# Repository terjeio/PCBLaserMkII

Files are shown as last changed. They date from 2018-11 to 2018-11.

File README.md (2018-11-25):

## BluRay Laser PCB exposer

---

### Design criteria:

160 x 100mm exposure area \(Eurocard\).
Able to render at least down to 0.25mm \(10 mil, 250um\) track/track separation.
Easy workflow.

### Vector vs. raster plotting:

Vector plotting requires parsing of a vector format to control the drive mechanism,
most PCB-design packages are able to output the design in Gerber and/or HPGL-formats.

Raster plotting is similar to inkjet printing, the laser is fired for the individual pixels.

I decided to use raster plotting since this is relatively simple to implement.

By using the belt calculator available at [buildlog.net](http://buildlog.net/cnc_laser/belt_calcs.htm) I found that
17 teeth pulleys and 8 microsteps would result in a resolution of 1195.297 steps per inch, which is pretty close to 1200 dpi \(21.250 um/step\). Near enough for hobby use, resolution may be adjusted when generating the bitmap file to match the actual resolution if a perfect match is required.

### Photosentive PCBs:

I had some blank PCBs lying around so I wanted to try Dupont Riston dry-film photoresist.
This has optimal sensitivity in the 350-380nm range, and may be exposed by 405nm as there is some sensitivity up to 450nm.
Lines and spaces achievable:
In optimized production environment: 75um/3mil
In lab environment: 50um/2mil

The (teoretical) resolution of the design is thus somewhat better than the resolution of the film.

### Workflow for KiCad EDA:

Plot the design to PDF in 1:1 format. Print resulting files via PDFCreator to PNG-format files, I use 4bpp in order to avoid artefacts in the bitmap.

### Firmware:

[Firmware](https://github.com/terjeio/PCBLaserFirmvare/) is provided for [MSP430G2553 LaunchPad](http://www.ti.com/tool/MSP-EXP430G2) or MSP430F5310 on a [custom PCB](Electrical/Controller). The MSP430F5310 is slightly faster and has more RAM, useful for buffering. It also supports adjusting the laser power via the [desktop application](https://github.com/terjeio/PCBLaserDesktopApp).

Firmware may be compiled in the [cloud](https://dev.ti.com), there is no need to install a local IDE.

### Hackaday project:

[PCB Exposer](https://hackaday.io/project/26216-pcb-exposer)

### Improvements:

A closed design with an interlocked door to block reflections from the laser. The published version is an open design, **ALWAYS** use protective eyewear when operating the exposer!

Laser cut acrylic bed? My prototype has an aluminium bed that requires access to a mill to fabricate. 

---

BOM:
<pre>
3 SC6UU 25x30x18 polymer bearing in aluminium housing
2 LM6UU 5x10x14 polymer bearing (or Oilite sintered bronze bearings)
4 6mm ground shafts, 300mm
2 3mm ground shafts or similar, 25mm for the belt idlers
1 3D printed laser carrier, FreeCAD design provided
1 diode housing 13x16x15,5
1 lens 405nm 8mm focal length?
1 405nm laser diode, 100mW
2 Nema 17 stepper motors, max 34mm long
2 17T pulleys
2 idlers to match the pulleys
  GT2 6mm belt, approx. 1m
  6mm acrylic for laser cut case, dxf-files provided
  4mm acrylic for laser cut case, dxf-files provided
1 MSP430G2553 LaunchPad or custom controller PCB (design included). Please refer to schematics for BOM for the latter.
1 laser driver PCB (design included). Please refer to schematics for BOM.
</pre>

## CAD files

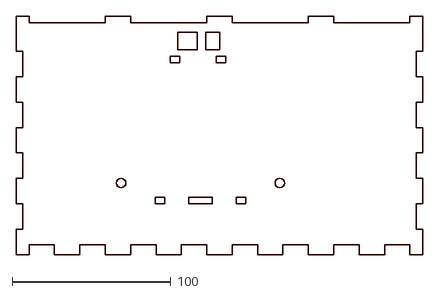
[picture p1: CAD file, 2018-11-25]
Mechanical/Back 4mm.dxf
256.0 x 150.0

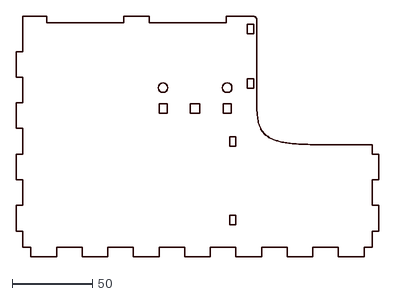
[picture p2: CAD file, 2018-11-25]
Mechanical/Left side 4mm.dxf
226.0 x 150.0

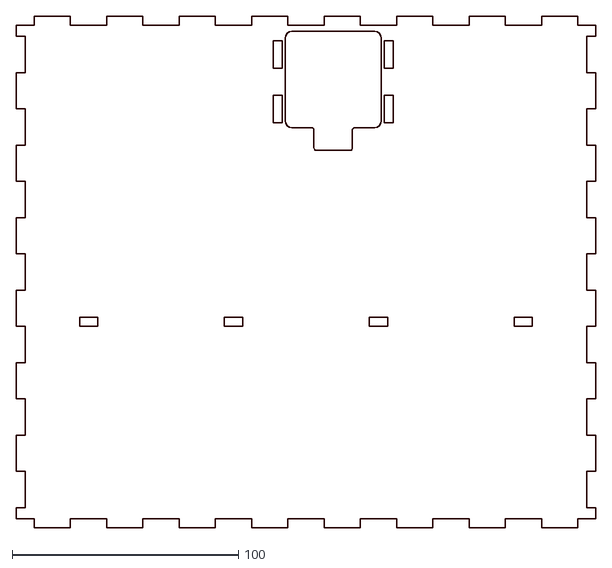
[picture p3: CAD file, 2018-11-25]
Mechanical/Base 6mm.dxf
256.0 x 226.0

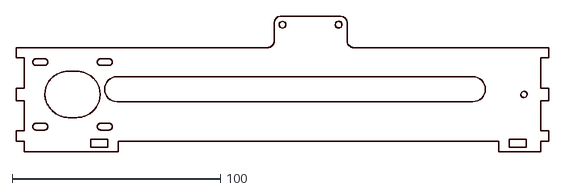
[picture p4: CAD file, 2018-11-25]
Mechanical/X-motor bracket 6mm.dxf
256.0 x 65.0

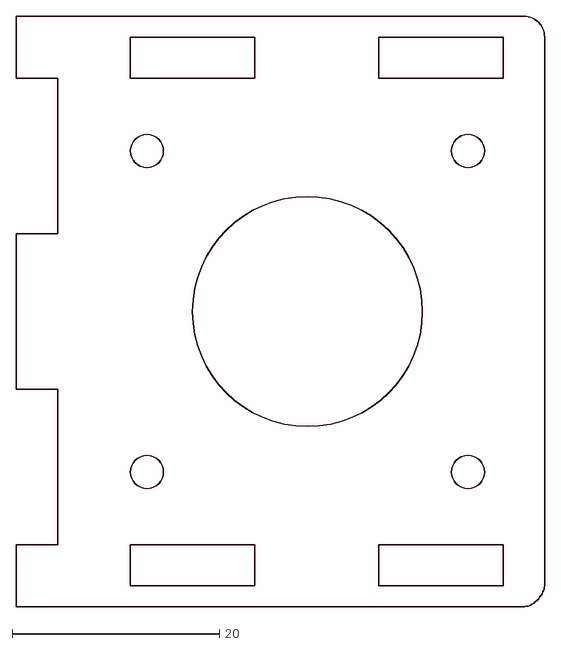
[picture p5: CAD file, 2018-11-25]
Mechanical/Y-motor bracket top 4mm.dxf
51.0 x 57.0

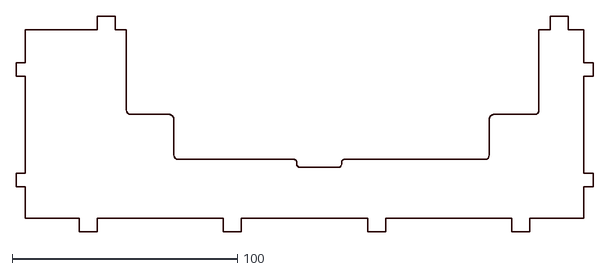
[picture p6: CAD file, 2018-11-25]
Mechanical/Wall stiffener 4mm.dxf
256.0 x 95.5

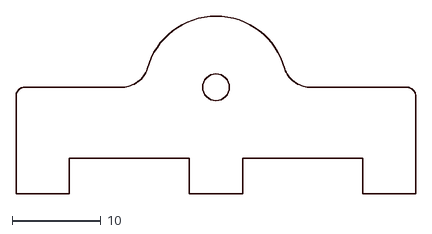
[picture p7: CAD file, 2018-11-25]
Mechanical/X-idler holder 4mm.dxf
45.0 x 20.0

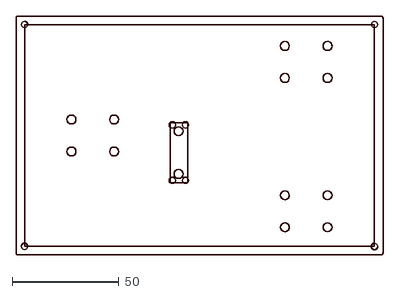
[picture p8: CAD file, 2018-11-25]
Mechanical/Alu bed.dxf
172.0 x 112.0

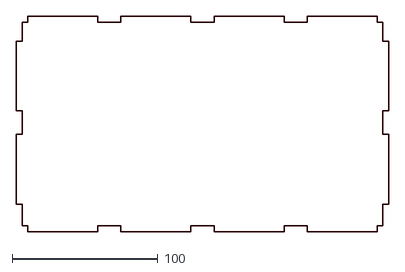
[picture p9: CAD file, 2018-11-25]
Mechanical/Top 4mm.dxf
256.0 x 148.0

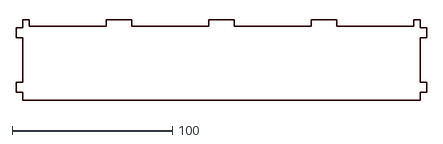
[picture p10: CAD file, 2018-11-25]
Mechanical/Front recessed 4mm.dxf
256.0 x 50.0

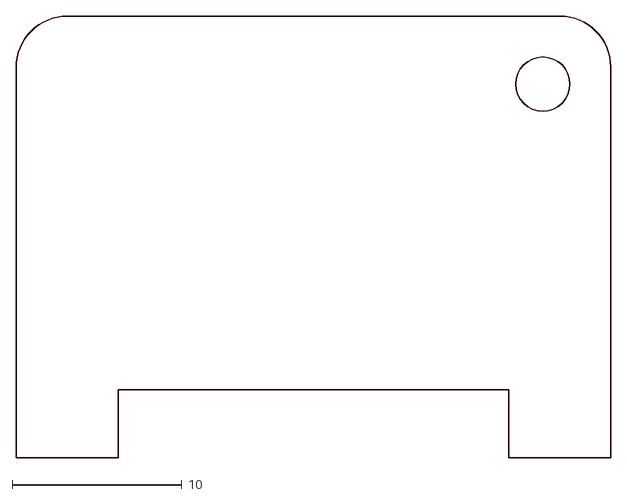
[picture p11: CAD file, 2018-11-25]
Mechanical/PCB bracket 4mm.dxf
35.0 x 26.0

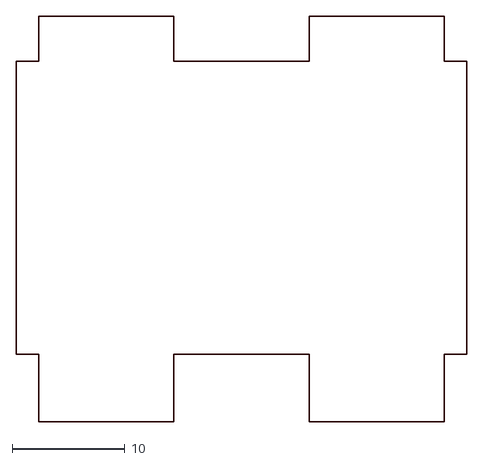
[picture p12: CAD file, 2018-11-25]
Mechanical/Y-motor bracket side 4mm (x2).dxf
40.0 x 36.0

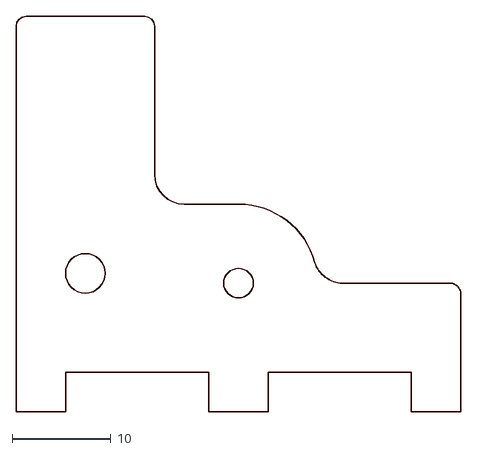
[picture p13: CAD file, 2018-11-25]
Mechanical/Y-idler holder #1 4mm.dxf
45.0 x 40.0

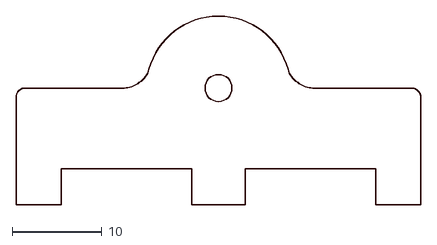
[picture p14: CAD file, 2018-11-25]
Mechanical/Y-idler holder #2 4mm.dxf
45.0 x 21.0

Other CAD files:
Mechanical/Right side 4mm.dxf
Mechanical/laser head.FCStd
Mechanical/Front 4mm.dxf

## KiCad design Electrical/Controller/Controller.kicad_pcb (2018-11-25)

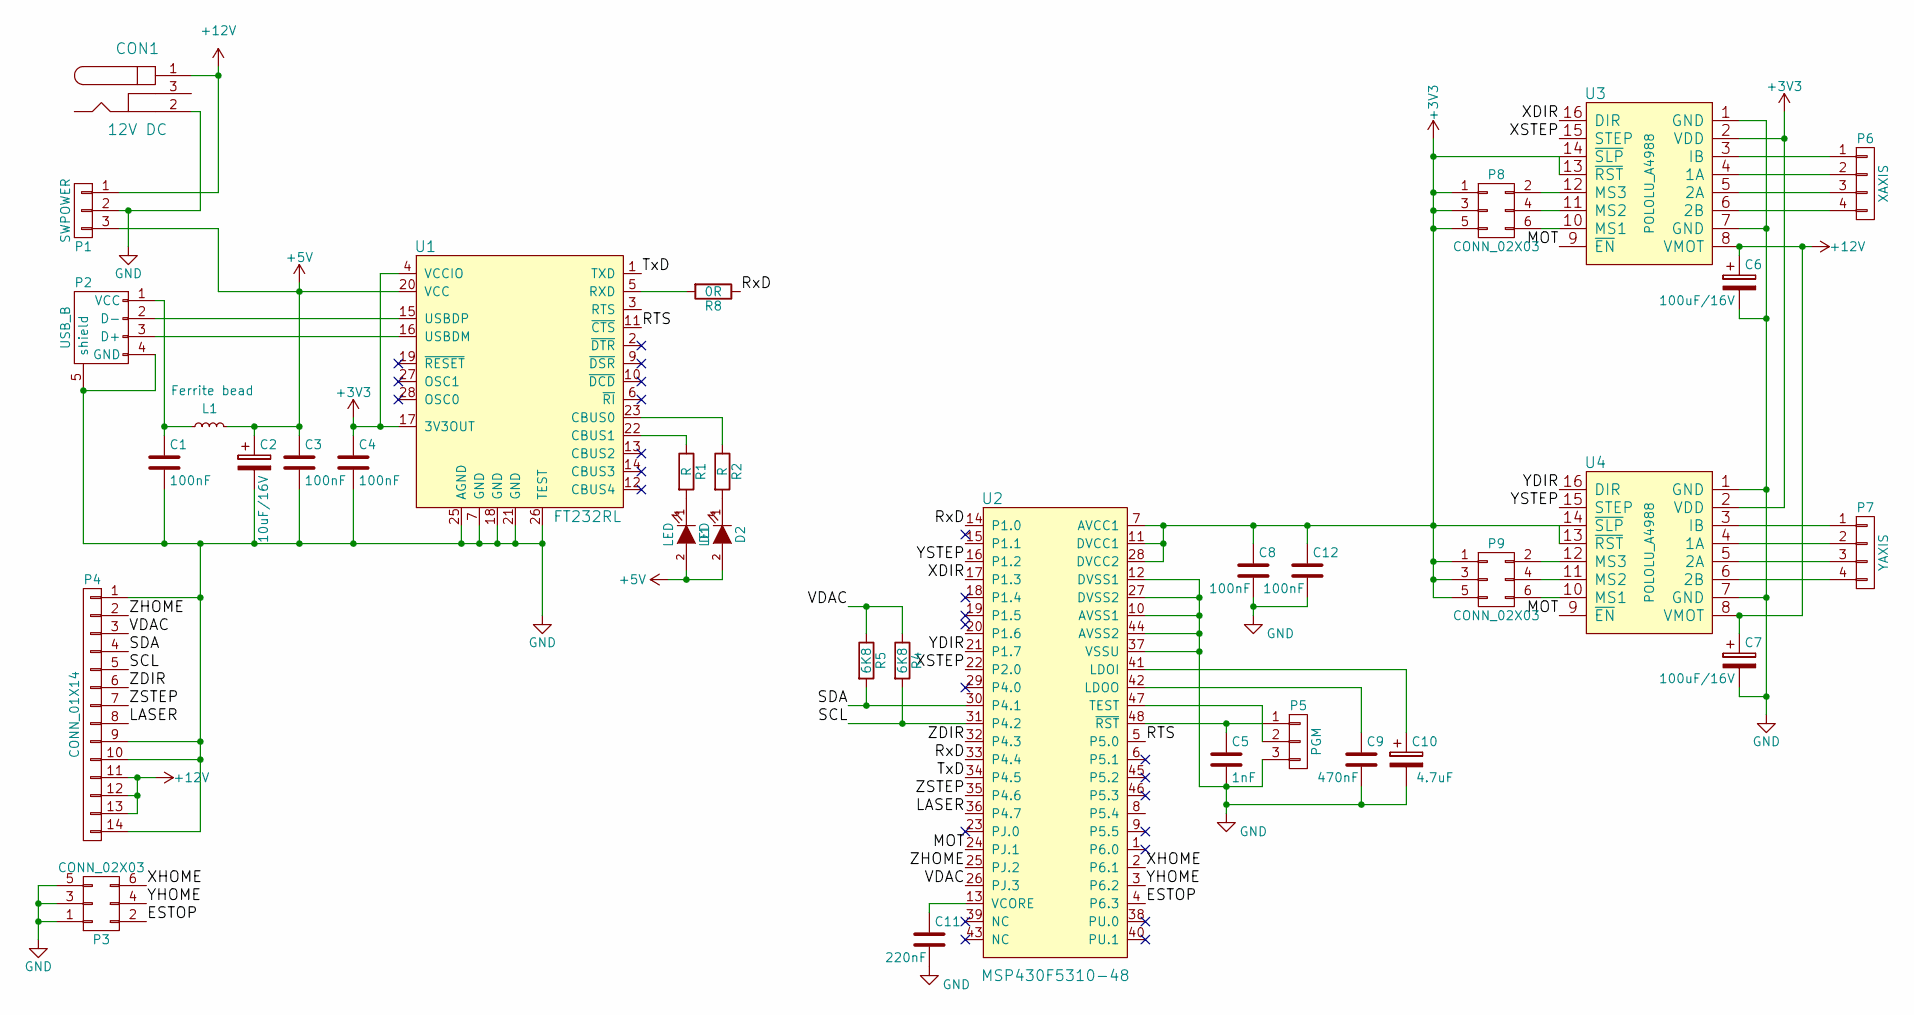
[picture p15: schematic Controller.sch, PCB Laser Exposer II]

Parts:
C1, C3, C4, C8, C12: 100nF; C_0805
C2: 10uF/16V; CP_Tantalum_Case-A_EIA-3216-18_Reflow
C5: 1nF; C_0805
C6, C7: 100uF/16V; CP_Radial_D8.0mm_P3.50mm
C9: 470nF; C_0805
C10: 4.7uF; CP_Tantalum_Case-A_EIA-3216-18_Reflow
C11: 220nF; C_0805
CON1: 12V DC; BARREL_JACK
D1, D2: LED; LED_1206
L1: Ferrite bead; R_0805
P1: SWPOWER; Pin_Header_Straight_1x03_Pitch2.54mm
P2: USB_B
P3, P8, P9: CONN_02X03; Pin_Header_Straight_2x03_Pitch2.54mm
P4: CONN_01X14; MOLEX_52271-1279
P5: PGM; Pin_Header_Straight_1x03_Pitch2.54mm
P6: XAXIS; Pin_Header_Straight_1x04_Pitch2.54mm
P7: YAXIS; Pin_Header_Straight_1x04_Pitch2.54mm
R1, R2: R; R_0805
R4, R5: 6K8; R_0805
R8: 0R; R_0805
U1: FT232RL; SSOP-28_5.3x10.2mm_Pitch0.65mm
U2: MSP430F5310-48; TQFP-48_7x7mm_Pitch0.5mm
U3, U4: POLOLU_A4988; Polulu_A4988

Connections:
+3V3: C4.1, C8.1, C12.1, P8.1, P8.3, P8.5, P9.1, P9.3, P9.5, U1.4 (VCCIO), U1.17 (3V3OUT), U2.7 (AVCC1), U2.11 (DVCC1), U2.28 (DVCC2), U3.2 (VDD), U3.13 (~RST), U3.14 (~SLP), U4.2 (VDD), U4.13 (~RST), U4.14 (~SLP)
+5V: C2.1, C3.1, D1.2 (A), D2.2 (A), L1.2, P1.3, U1.20 (VCC)
+12V: C6.1, C7.1, CON1.1, P1.1, P4.11, P4.12, P4.13, U3.8 (VMOT), U4.8 (VMOT)
/ESTOP: P3.2, U2.4 (P6.3)
/LASER: P4.8, U2.36 (P4.7)
/MOT: U2.24 (PJ.1), U3.9 (~EN), U4.9 (~EN)
/RTS: U1.11 (~CTS), U2.5 (P5.0)
/RxD: R8.1, U2.14 (P1.0), U2.33 (P4.4)
/SCL: P4.5, R4.2, U2.31 (P4.2)
/SDA: P4.4, R5.2, U2.30 (P4.1)
/TxD: U1.1 (TXD), U2.34 (P4.5)
/VDAC: P4.3, R4.1, R5.1, U2.26 (PJ.3)
/XDIR: U2.17 (P1.3), U3.16 (DIR)
/XHOME: P3.6, U2.2 (P6.1)
/XSTEP: U2.22 (P2.0), U3.15 (STEP)
/YDIR: U2.21 (P1.7), U4.16 (DIR)
/YHOME: P3.4, U2.3 (P6.2)
/YSTEP: U2.16 (P1.2), U4.15 (STEP)
/ZDIR: P4.6, U2.32 (P4.3)
/ZHOME: P4.2, U2.25 (PJ.2)
/ZSTEP: P4.7, U2.35 (P4.6)
GND: C1.2, C2.2, C3.2, C4.2, C5.2, C6.2, C7.2, C8.2, C9.2, C10.2, C11.2, C12.2, CON1.2, P1.2, P2.4 (GND), P2.5 (shield), P3.1, P3.3, P3.5, P4.1, P4.9, P4.10, P4.14, P5.3, U1.7 (GND), U1.18 (GND), U1.21 (GND), U1.25 (AGND), U1.26 (TEST), U2.10 (AVSS1), U2.12 (DVSS1), U2.27 (DVSS2), U2.37 (VSSU), U2.44 (AVSS2), U3.1 (GND), U3.7 (GND), U4.1 (GND), U4.7 (GND)
NC: U1.8 (NC)
unnamed: C1.1, L1.1, P2.1 (VCC)
unnamed: C5.1, P5.1, U2.48 (~RST)
unnamed: C9.1, U2.42 (LDOO)
unnamed: C10.1, U2.41 (LDOI)
unnamed: C11.1, U2.13 (VCORE)
unnamed: D1.1 (K), R1.2
unnamed: D2.1 (K), R2.2
unnamed: P5.2, U2.47 (TEST)
unnamed: P6.1, U3.3 (IB)
unnamed: P6.2, U3.4 (1A)
unnamed: P6.3, U3.5 (2A)
unnamed: P6.4, U3.6 (2B)
unnamed: P7.1, U4.3 (IB)
unnamed: P7.2, U4.4 (1A)
unnamed: P7.3, U4.5 (2A)
unnamed: P7.4, U4.6 (2B)
unnamed: P8.2, U3.12 (MS3)
unnamed: P8.4, U3.11 (MS2)
unnamed: P8.6, U3.10 (MS1)
unnamed: P9.2, U4.12 (MS3)
unnamed: P9.4, U4.11 (MS2)
unnamed: P9.6, U4.10 (MS1)
unnamed: R1.1, U1.22 (CBUS1)
unnamed: R2.1, U1.23 (CBUS0)
unnamed: R8.2, U1.5 (RXD)

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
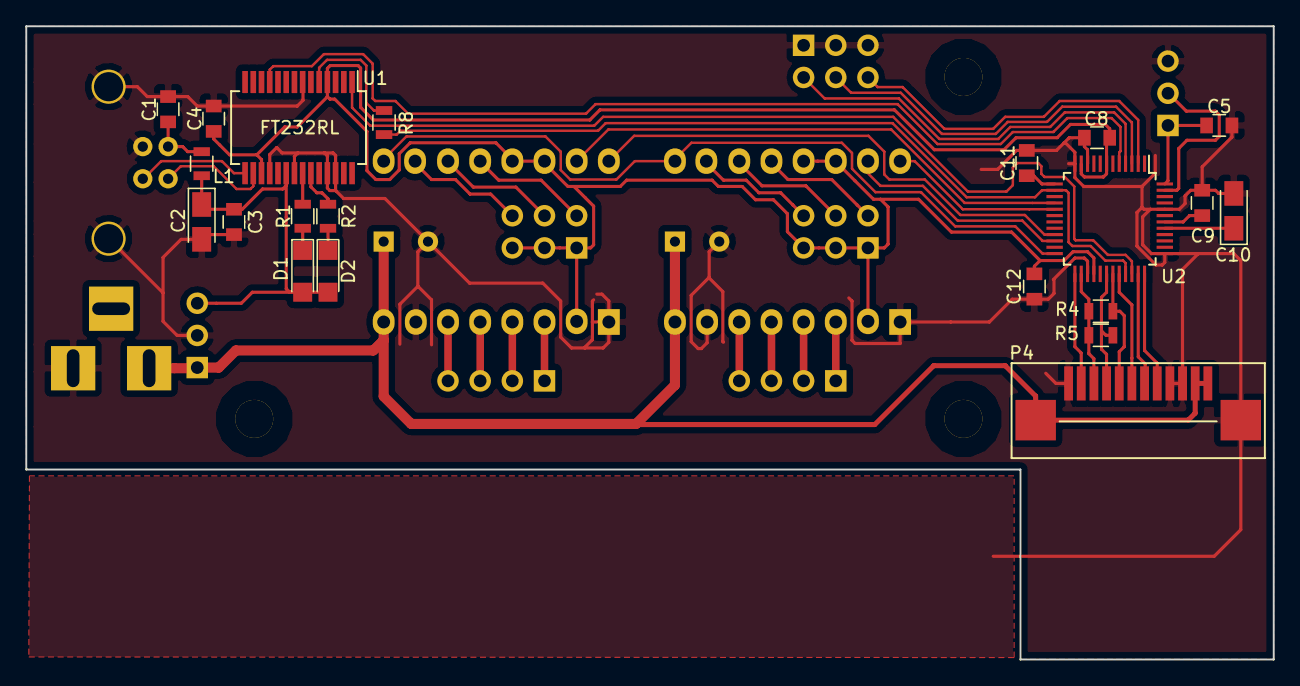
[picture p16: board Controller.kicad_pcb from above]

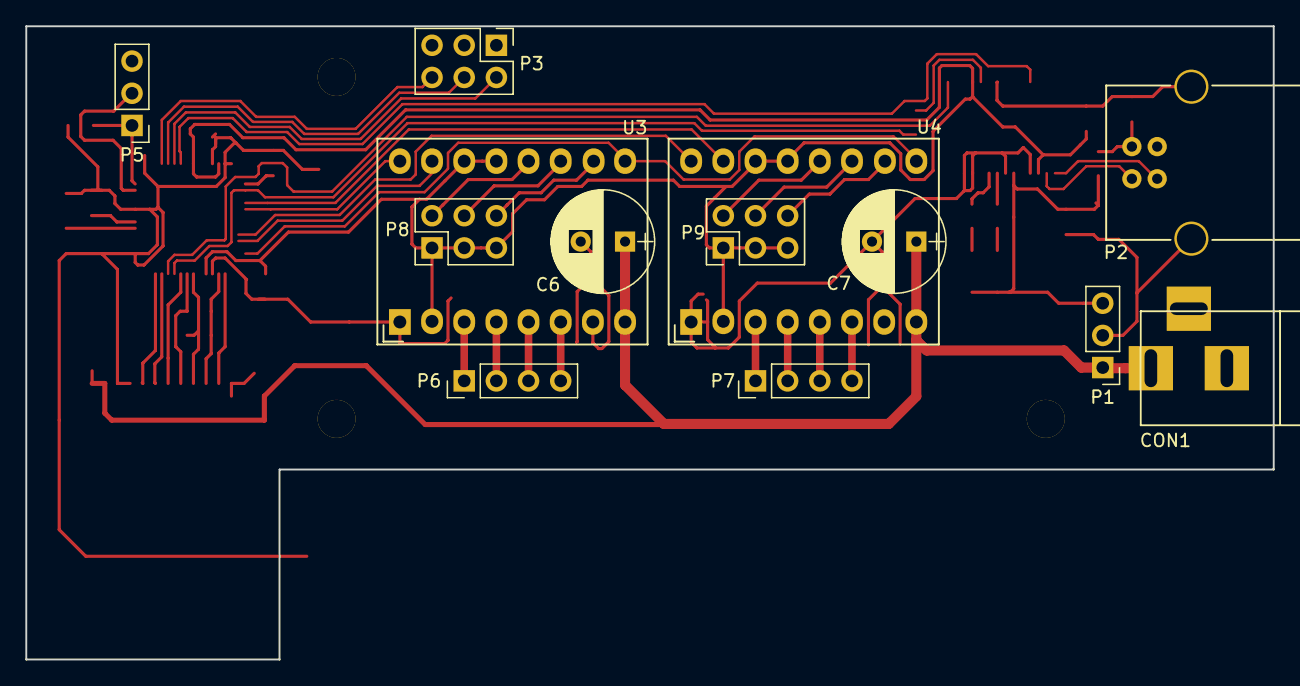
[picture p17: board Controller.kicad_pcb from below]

Board: 2 copper layers, 98.5 x 50.0 mm, 34 parts (13 on the bottom side), 49 nets.

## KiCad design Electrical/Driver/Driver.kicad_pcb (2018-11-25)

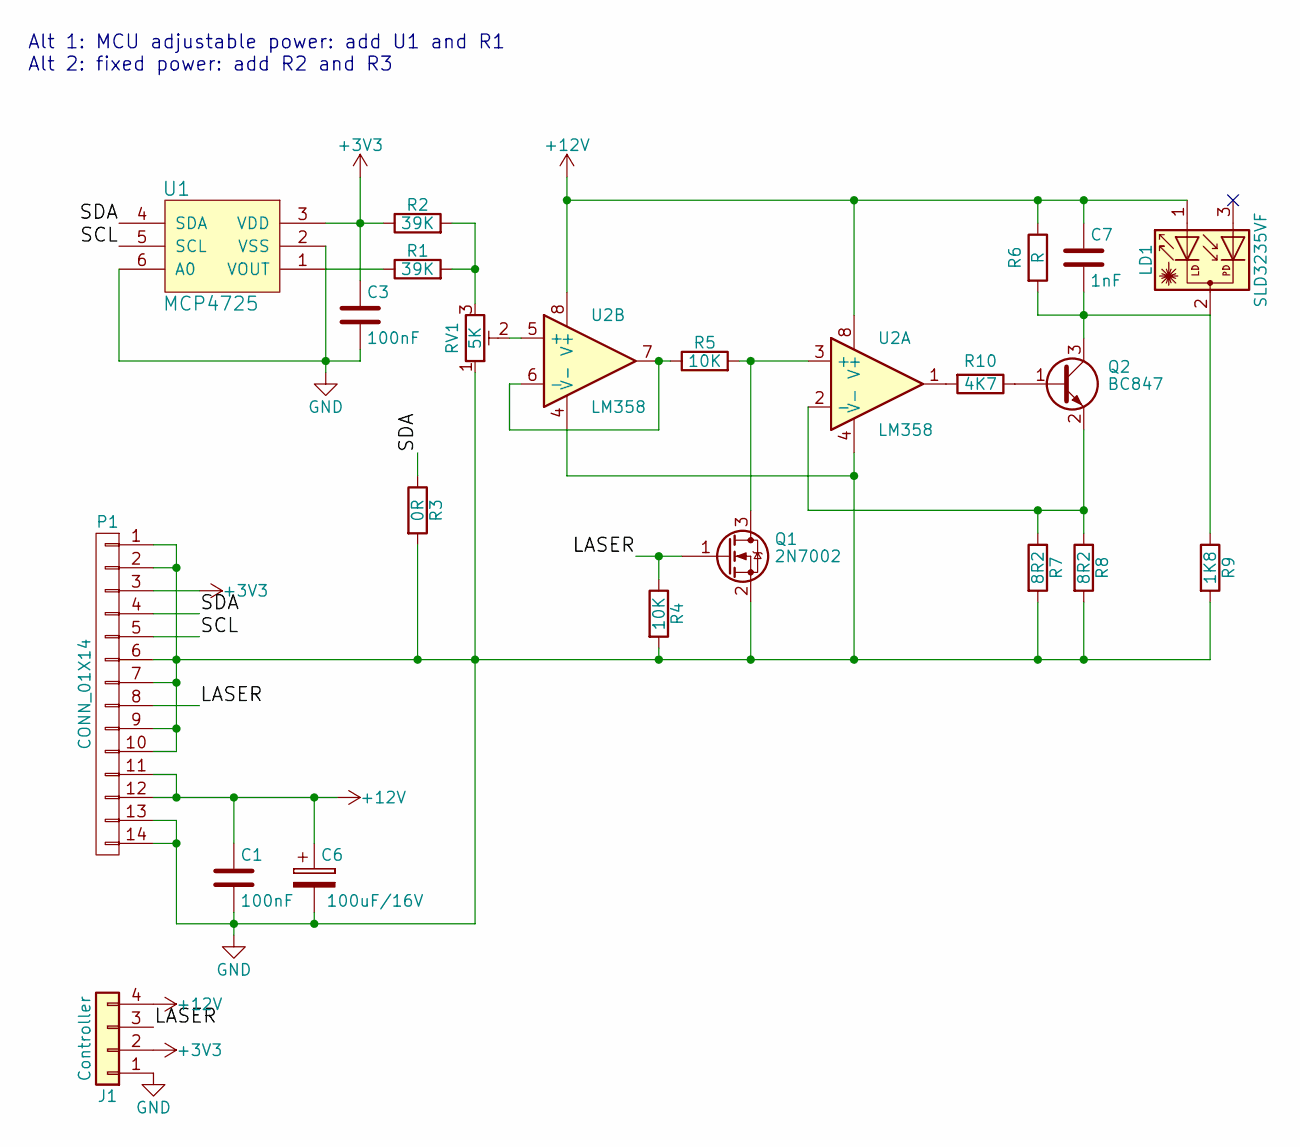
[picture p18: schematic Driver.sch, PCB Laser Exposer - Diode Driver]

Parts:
C1: 100nF; C_1206
C3: 100nF; C_0805
C6: 100uF/16V; CP_Elec_5x4.5
C7: 1nF; C_1206
J1: Controller; Pin_Header_Straight_1x04_Pitch2.54mm
LD1: SLD3235VF; TO-18-3_Laser_brass_host
P1: CONN_01X14; MOLEX_52271-1279
Q1: 2N7002; SOT-23
Q2: BC847; SOT-23
R1, R2: 39K; R_0805
R3: 0R; R_0805
R4, R5: 10K; R_0805
R6: R; R_0805
R7, R8: 8R2; R_1206
R9: 1K8; R_0805
R10: 4K7; R_0805
RV1: 5K; Potentiometer_Trimmer_Bourns_3296P
U1: MCP4725; SOT-23-6
U2: LM358; SOIC-8_3.9x4.9mm_Pitch1.27mm

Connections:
+3V3: C3.1, J1.2, P1.3, R2.1, U1.3 (VDD)
+12V: C1.1, C6.1, C7.1, J1.4, LD1.1, P1.11, P1.12, R6.1, U2.8 (V+)
/LASER: J1.3, P1.8, Q1.1 (G), R4.1
/SCL: P1.5, U1.5 (SCL)
/SDA: P1.4, R3.1, U1.4 (SDA)
GND: C1.2, C3.2, C6.2, J1.1, P1.1, P1.2, P1.6, P1.7, P1.9, P1.10, P1.13, P1.14, Q1.2 (S), R3.2, R4.2, R7.2, R8.2, R9.2, RV1.1, U1.2 (VSS), U1.6 (A0), U2.4 (V-)
unnamed: C7.2, LD1.2, Q2.3 (C), R6.2, R9.1
unnamed: Q1.3 (D), R5.2, U2.3 (+)
unnamed: Q2.1 (B), R10.1
unnamed: Q2.2 (E), R7.1, R8.1, U2.2 (-)
unnamed: R1.1, U1.1 (VOUT)
unnamed: R1.2, R2.2, RV1.3
unnamed: R5.1, U2.6 (-), U2.7
unnamed: R10.2, U2.1
unnamed: RV1.2, U2.5 (+)

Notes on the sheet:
Alt 1: MCU adjustable power: add U1 and R1 Alt 2: fixed power: add R2 and R3

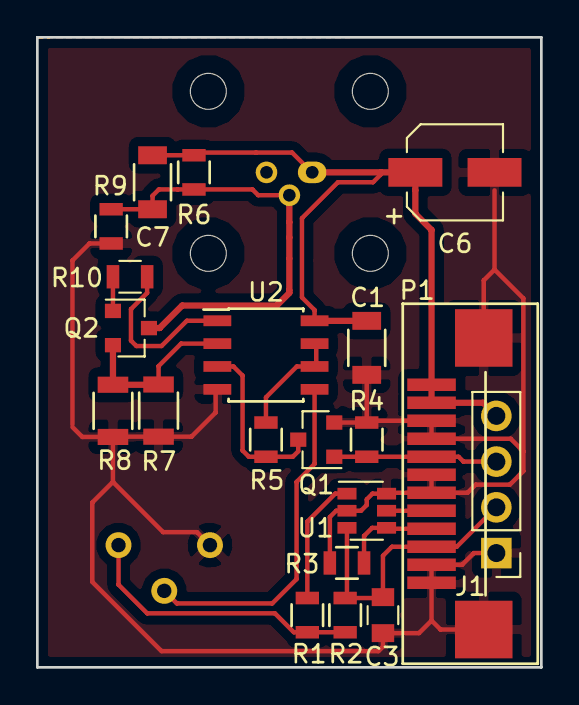
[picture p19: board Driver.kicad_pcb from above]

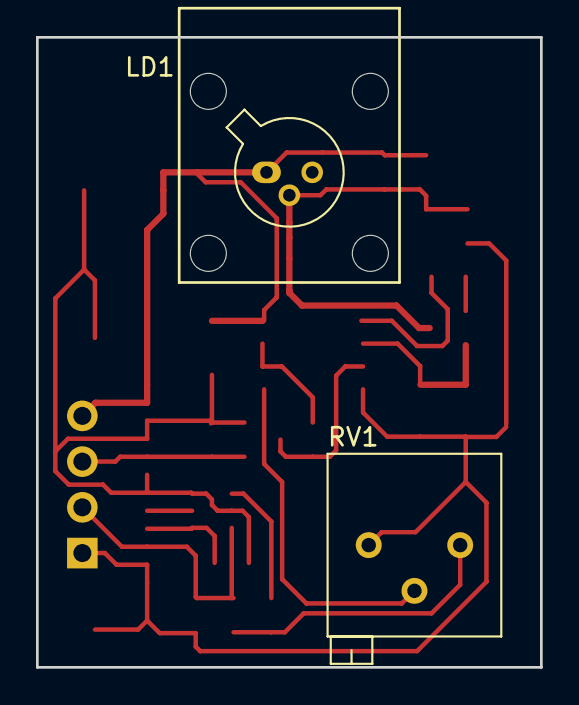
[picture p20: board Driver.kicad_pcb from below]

Board: 2 copper layers, 28.0 x 35.0 mm, 22 parts (2 on the bottom side), 15 nets.

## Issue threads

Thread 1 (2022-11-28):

Missing R6 value

breezer15, 2022-11-28:
Hi, I want to rebuild this great project. My problem is the missing R6 resistor value for the laser driver. What ist the correct resistor value?

terjeio, 2022-12-02:
I do not have KiCad installed (I am on holiday) so cannot check the schematic.
IIRC R6 is in parallell with the diode? If so it is not to be mounted.

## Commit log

2017-09-17 Initial commit of tentative design
    [Laser Carriage.FCStd]
2018-11-25 Design files used for prototype #2
    [Alu bed.dxf, Back 4mm.dxf, Base 6mm.dxf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]

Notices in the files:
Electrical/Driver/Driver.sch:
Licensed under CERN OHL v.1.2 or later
